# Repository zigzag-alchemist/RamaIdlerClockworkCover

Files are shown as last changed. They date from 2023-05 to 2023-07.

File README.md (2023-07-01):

# Rama Idler Clockwork Cover
This is a mod of the [Rama front idlers](https://github.com/Ramalama2/Voron-2-Mods/tree/main/Front_Idlers) for the Voron 2.4. 

Its purpose is to keep the two tensioning screws synchronized by connecting them via a spur gear assembly in a housing cover.

The profile of the idler is identical to the original Rama idlers, however the mod takes an extra 4mm of space towards the doors of the printer for the gear assembly and cover.

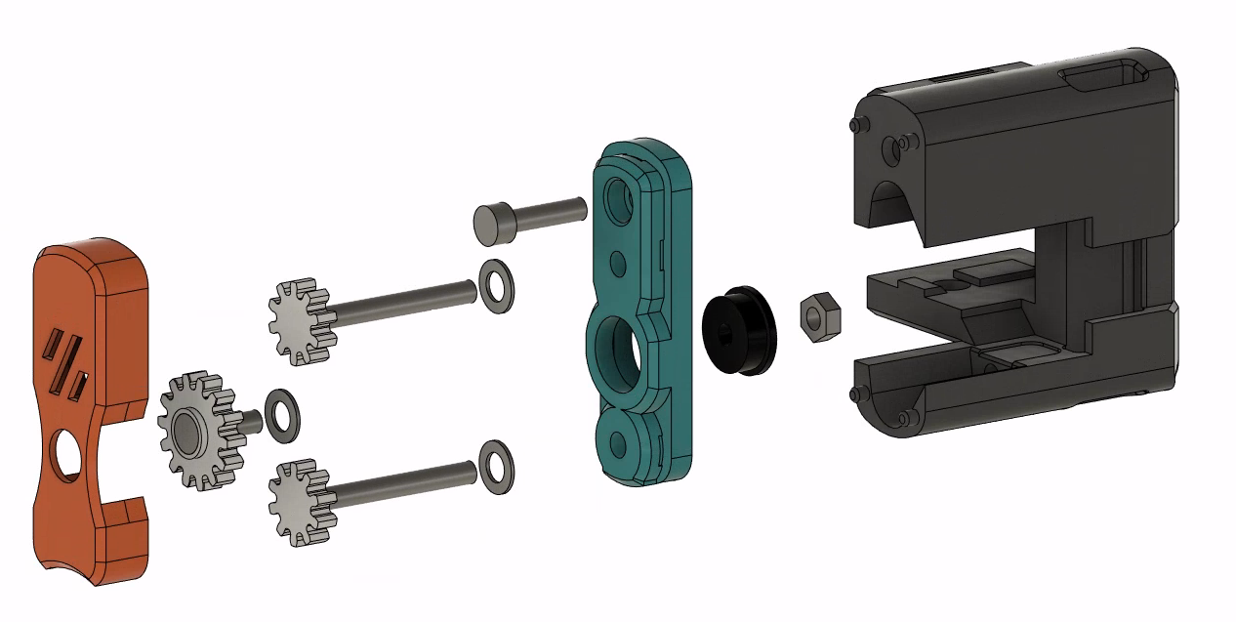
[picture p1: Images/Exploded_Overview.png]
Overview


https://github.com/zigzag-alchemist/RamaIdlerClockworkCover/assets/133815727/17510b1a-aaa8-4d9a-9919-942fed6e33c1

# Warning!

This mod has had relatively little testing and is very experimental.

It has been running fine in my machine (~100hrs of print time, 2 tensioning cycles) but there may still be dragons lurking.

# Printed Parts

- Print with the standard Voron settings:
  - No supports required.
  - Parts should already be orientated correctly for printing.
- The `N` in `[partname]_xN.stl` denotes the number of copies required for both left and right idlers. No mirroring is required, the part is simply rotated for the left and right idlers to work with the lower and upper belts on both sides (same as the rama mod itself). `[a]_` is for an optional accented color scheme.
- The `Housing_Cover_x2.stl` is the only printed part which replaces a part of the stock Rama Idler (the [Front-Idlers\_Housing-Cover.stl](https://github.com/Ramalama2/Voron-2-Mods/blob/main/Front_Idlers/Voron%202.4/STL/Front-Idlers_Housing-Cover.stl)).
- You probably only need one of the `HexNut_Tool` options. The `Short` version may be more useful if the idler is already mounted and you only have room on one side, but the regular version is easier to use.

# BOM (For 2 idlers, on top of the standard Rama Idler BOM)

Quantity      | Description              | Notes
|:----------- |:------------------------ |:---------------------------------------------
2             | M3x12 SHCS               |
2             | M8x12 SHCS               |
4             | M3x30/40 Hexhead DIN 931 | Replaces the M3x30/40 SHCS in Rama Idler BOM
2             | M3 Hexnut                |
6             | M3 Washer                |
2             | F623-2RS bearing         |

# Instructions

1. Use the `HexNut_Tool_x1.stl` to press the F623-2RS into both `Housing_Cover_x2.stl`

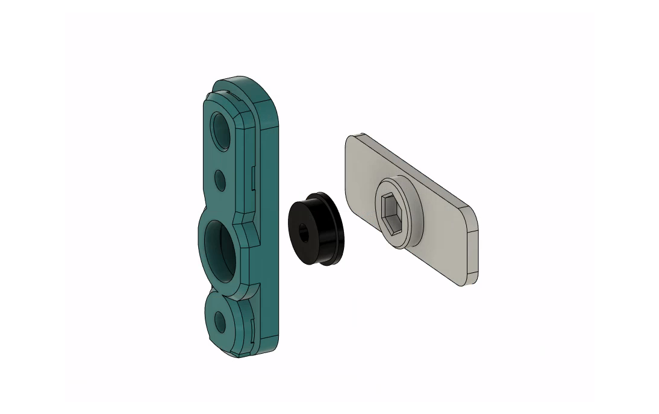
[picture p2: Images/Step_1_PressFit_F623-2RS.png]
Step_1


2. Complete the rest of the Rama Idler and then install the `Housing_Cover_x2.stl`
  with a M3x12SHCS. *Careful not to overtighten, it threads into plastic*

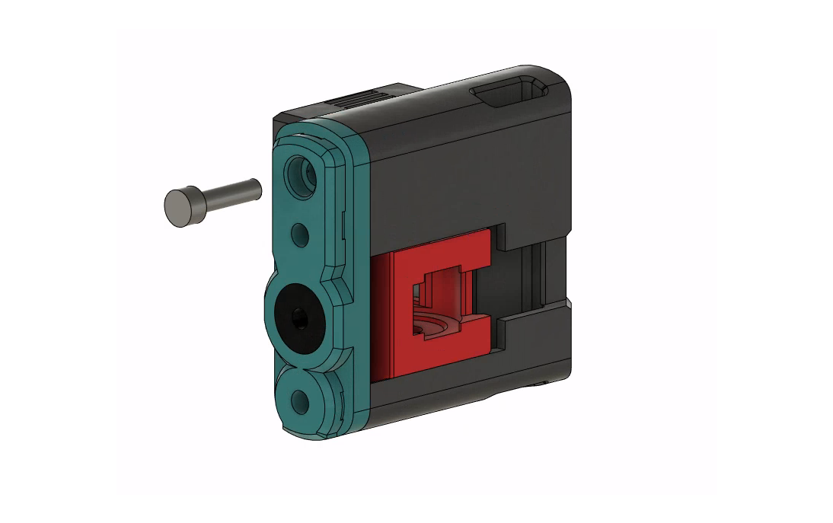
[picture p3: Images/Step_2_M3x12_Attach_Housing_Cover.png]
Step_2


3. Pressfit the M3x30 Hexagon head bolt into the `10T_Spur_Gear_Hex_x4.stl`. *The `Press_Fit_Jig_x1.stl` may be helpful for doing this with a vice or clamp.*

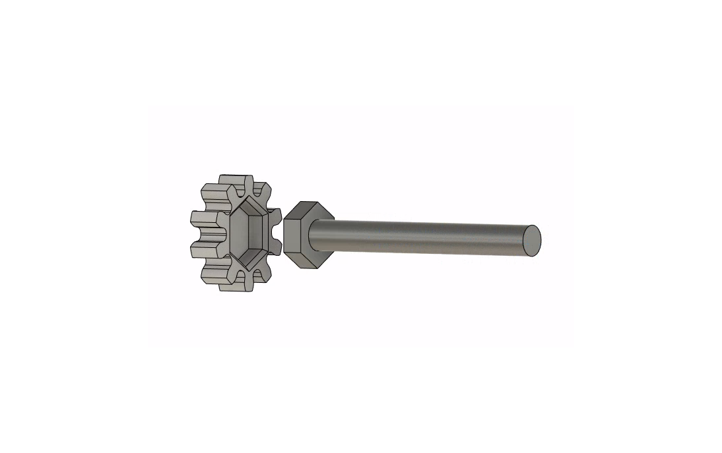
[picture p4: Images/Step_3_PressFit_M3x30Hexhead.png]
Step_3


4. Insert the 10T M3x30 spur gears into the Rama Idler housing
    1. For the convenience of Step 7, flip the `HexNut_Tool_x1.stl` and slot it into the house so the circular protrusion is facing the idler
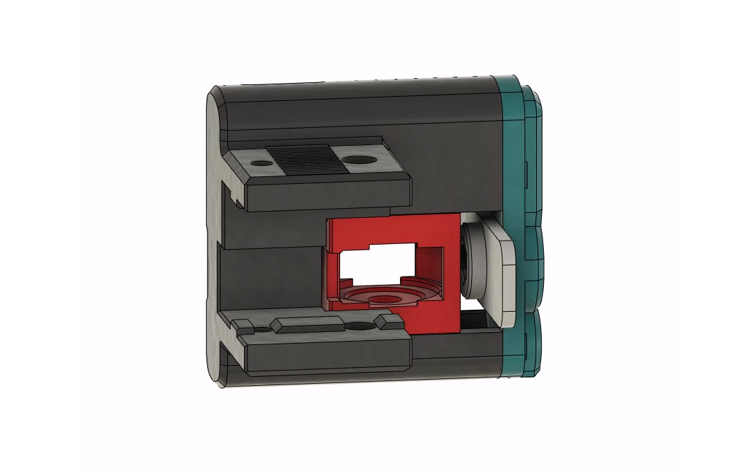
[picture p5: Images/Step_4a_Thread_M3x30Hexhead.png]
Step_4a

    2. Gently tighten the M3x30 spur gears with M3 washers until they both slightly tug the idler flat and even against the `HexNut_Tool_x1.stl`
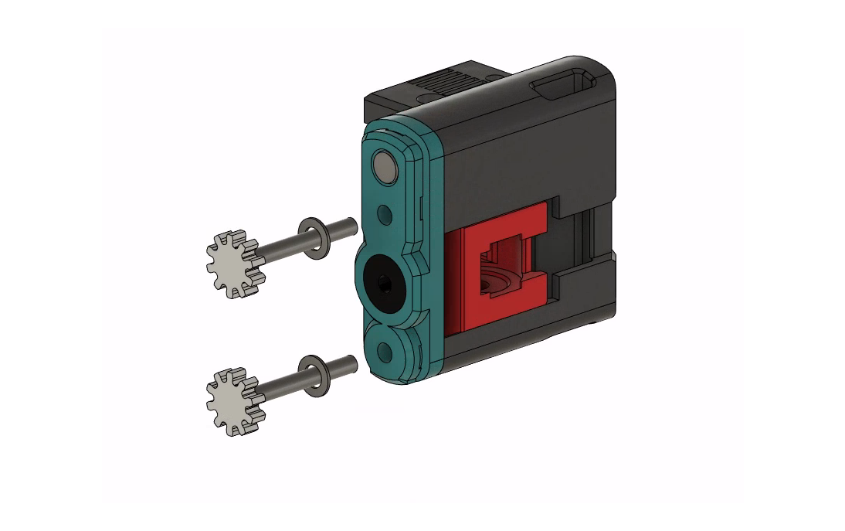
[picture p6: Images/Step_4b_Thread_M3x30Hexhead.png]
Step_4b


5. Use the `Press_Fit_Jig_x1.stl` to press the M3x8SHCS into the `14T_Control_Gear_x2.stl`
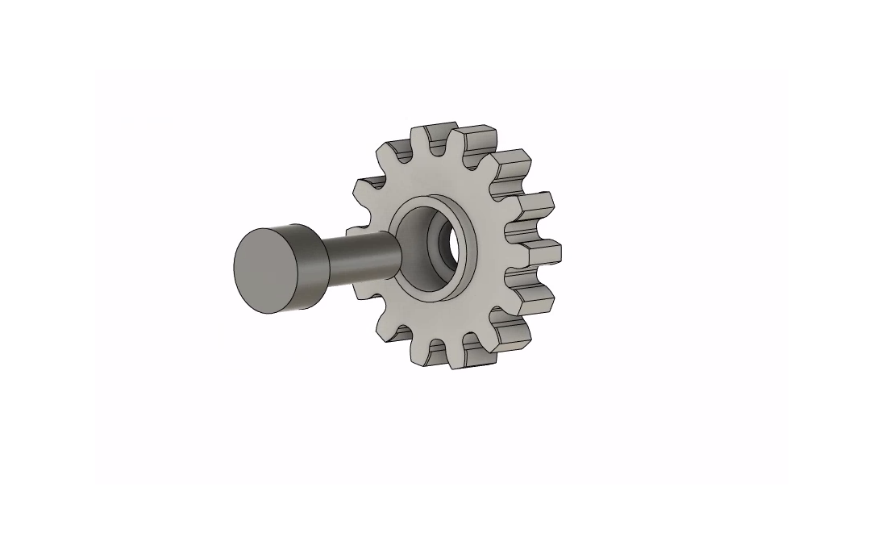
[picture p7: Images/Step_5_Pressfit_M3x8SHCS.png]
Step_5


6. Slide out the `HexNut_Tool_x1.stl` if it is still in the Rama housing, and insert an M3 hexnut
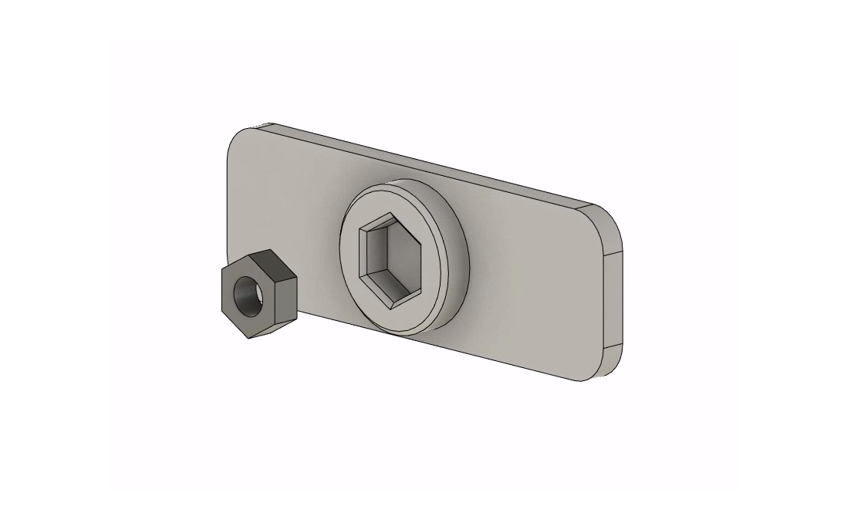
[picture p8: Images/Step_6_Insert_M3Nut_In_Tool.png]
Step_6


7. Attach the `14T_Control_Gear_x2.stl` to the bearing
    1. Insert the `HexNut_Tool_x1.stl` with the captured hexnut is facing the F623 bearing
    2. Screw the M3x8SHCS and `14T_Control_Gear_x2.stl` with an M3 washer through the F623 bearing and into the HexNut 
    3. Use the `HexNut_Tool_x1.stl` to prevent the hexnut from turning, and firmly tighten the M3x8SHCS
    4. *As you tighten the M3x8SHCS, the two 10T spur gears will tend to screw outwards, just keep pushing them back in and keep them engaged with the 14T gear. This is why we left room for the idler to move inwards in Step 4*

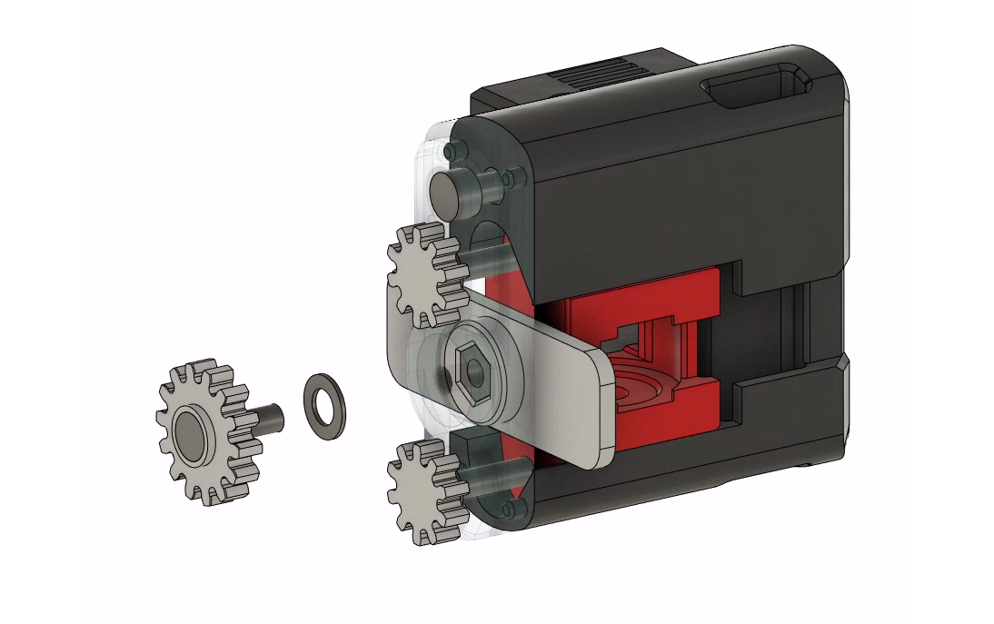
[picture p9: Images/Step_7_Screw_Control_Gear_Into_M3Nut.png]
Step_7


8.  The `[a]_Outer_Cover_x2.stl` has small catches and can simply be pressed on until you hear a click
    1. *Side Note: The `[a]_Outer_Cover_x2.stl` is there to prevent the 10T gears from screwing outwards when the belts are completely loosened. During normal operation with tension on the belts the `Outer_Cover.stl` is purely aesthetic and may indeed be left off entirely if so desired*
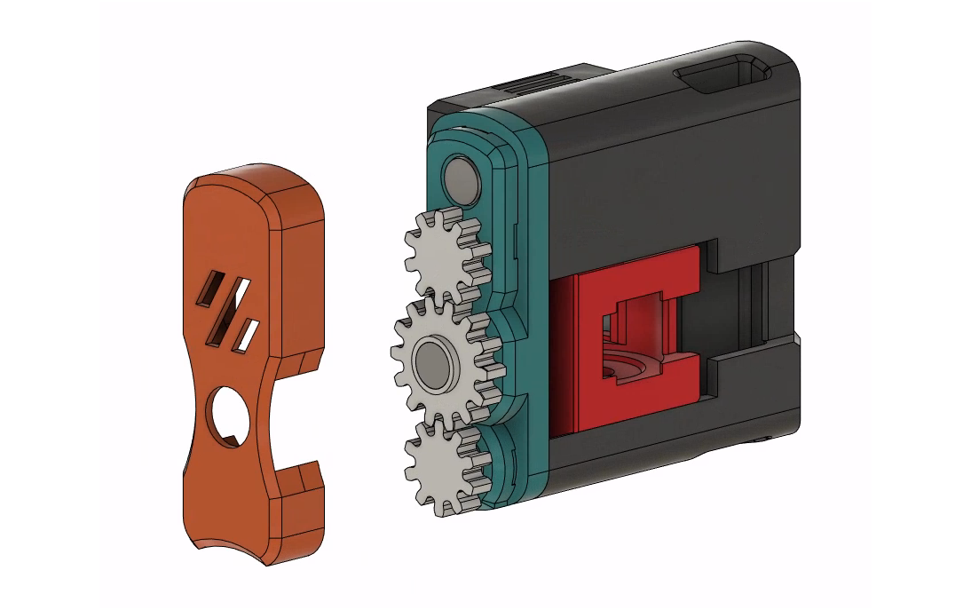
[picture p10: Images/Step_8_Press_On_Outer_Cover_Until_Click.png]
Step_8


9. To increase tension on the belts the exposed control screw must be turned anti-clockwise (and to decrease tension, clockwise). The gear mechanism reverses the tensioning direction from that of the standard Rama Idler

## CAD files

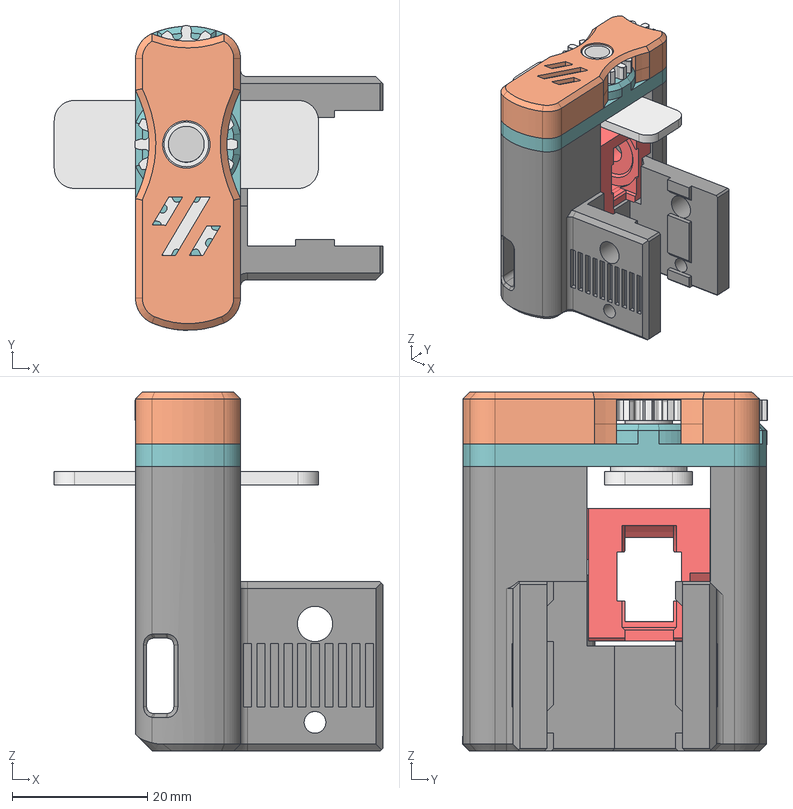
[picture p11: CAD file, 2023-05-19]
CAD/RamaIdlerClockworkCover.step
48.5 x 45.0 x 53.0 mm
Rama_Housing
Housing_Cover_x1
14T_Control_Gear_x1
10T_Spur_Gear_Hex_x2 x 2
M3Washer x 3
M3HexNut
F623-2RS Bearing
M3x8SHCS
HexNut_Tool_x1
[a]_Outer_Cover_x1
M3x30Hexhead x 2
M3x12SHCS
Rama_Idler

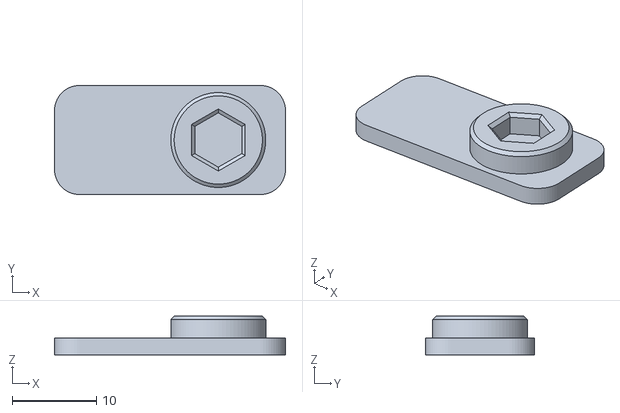
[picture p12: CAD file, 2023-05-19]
STL/HexNut_Tool_Short_x1.stl
27.5 x 13.0 x 4.60

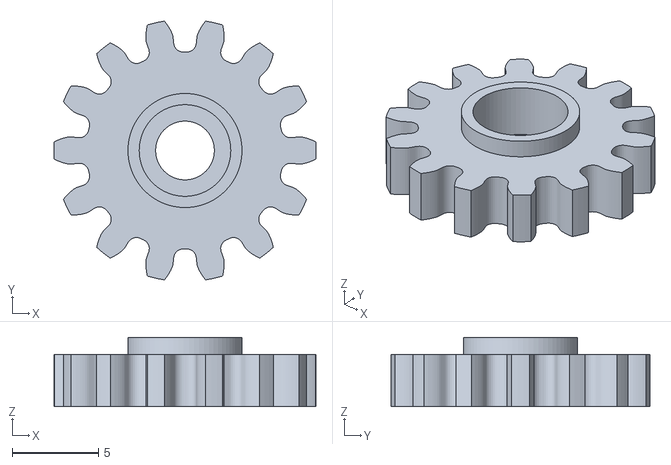
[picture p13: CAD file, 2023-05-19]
STL/14T_Control_Gear_x2.stl
15.2 x 15.0 x 4.00

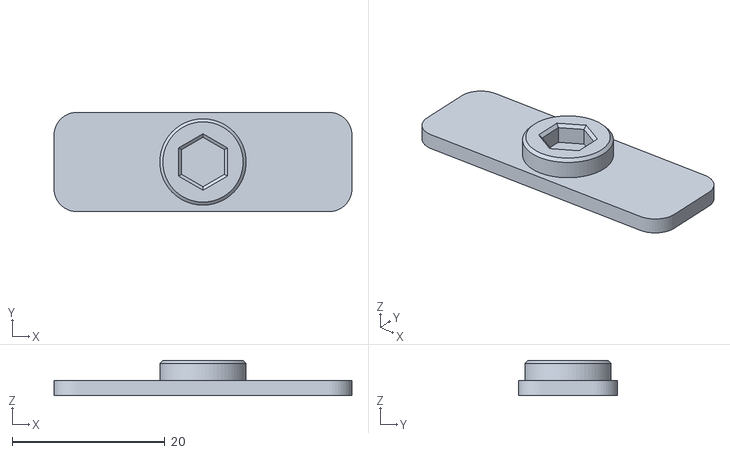
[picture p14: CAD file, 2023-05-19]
STL/HexNut_Tool_x1.stl
39.0 x 13.0 x 4.60

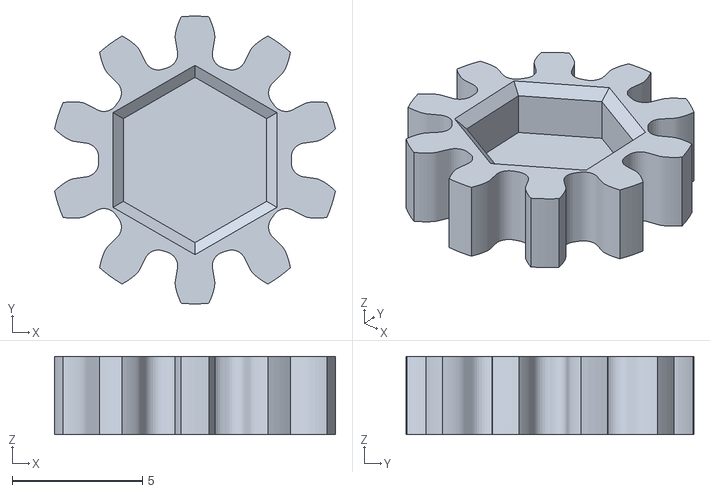
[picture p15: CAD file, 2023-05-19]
STL/10T_Spur_Gear_Hex_x4.stl
10.8 x 11.1 x 3.00

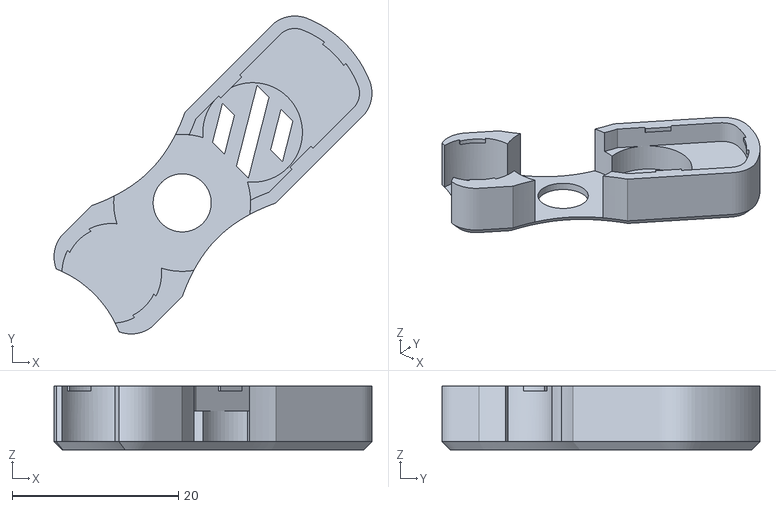
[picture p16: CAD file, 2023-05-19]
STL/[a]_Outer_Cover_x2.stl
38.3 x 38.3 x 7.70

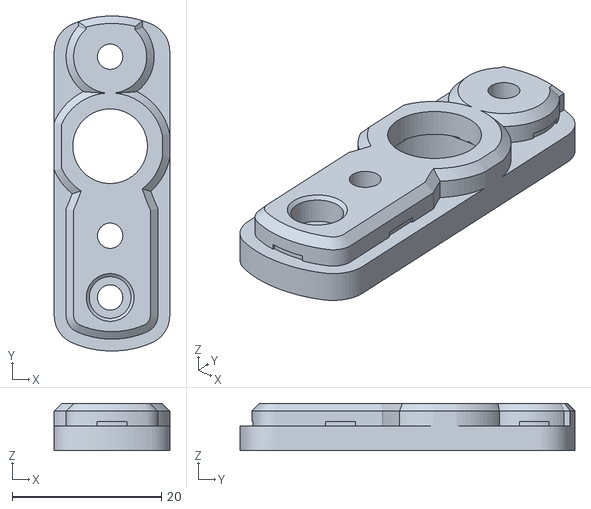
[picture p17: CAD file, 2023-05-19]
STL/Housing_Cover_x2.stl
15.5 x 44.9 x 6.30

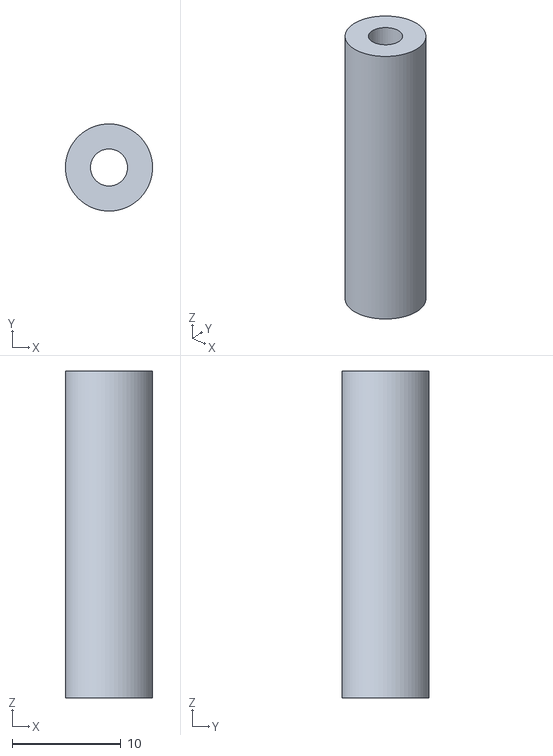
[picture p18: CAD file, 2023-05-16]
STL/Press_Fit_Jig_x1.stl
8.00 x 8.00 x 30.0

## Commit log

2023-05-19 Change design to single bearing control gear, hexhead for tensioning screws, and clip on outer cover
    [10T_Spur_Gear_Hex_x4.stl, 10T_Spur_Gear_x2.stl, 14T_Connecting_Spur_Gear_x1.stl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]
2023-05-19 Add short version of HexNut_Tool
    [HexNut_Tool_Short_x1.stl]
2023-07-01 Corrections and update
    [Housing_Cover_x2.stl, [a]_Outer_Cover_x2.stl]
2023-07-01 Clear old stls
    [Housing_Cover_B_x1.stl, [a]_Outer_Cover_B_x1.stl]
